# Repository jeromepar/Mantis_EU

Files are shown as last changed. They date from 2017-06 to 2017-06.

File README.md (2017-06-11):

# Mantis_EU

## CNC on a budget **(roughly 220€)**

-------------

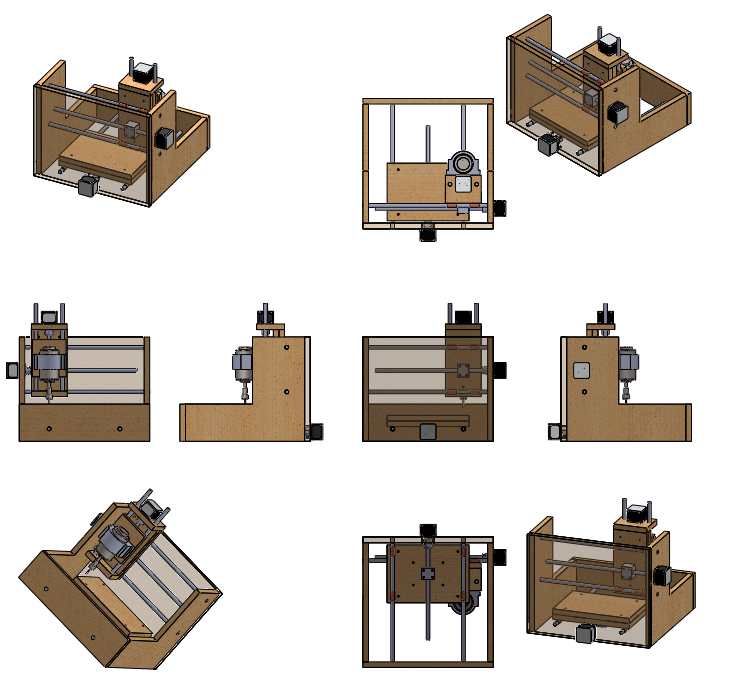
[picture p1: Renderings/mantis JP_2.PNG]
basic rendering


## Adaptation from the Mantis CNC design in order to build it in the EU (dimensions & providers)

### Key information:
- **__Total price around 220€__**
- 350*350mm frame
- *Work area of 100*220mm* (roughly an A5 sheet)
- Frame in 15mm plywood
- Using 3 Nema17 stepper motors
- Controled by an Arduino UNO hosting GRBL
- CNC shield by Protoneer [http://blog.protoneer.co.nz/arduino-cnc-shield/]

### This repository contains:
- CAD parts
- Some rendered pictures
- Some actual pictures
- the B.O.M.

### Basic required hardware:
- Drill press
- **a way to cut wood straight** (circular saw with guide, table circular saw, or jigsaw with skill)

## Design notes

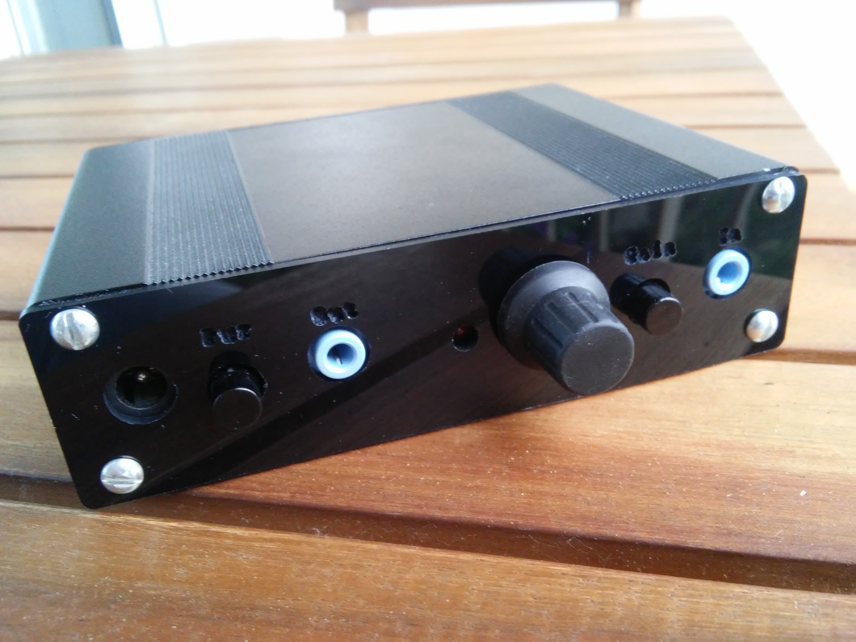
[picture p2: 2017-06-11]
Pictures/20170611_Project1_front_plate.jpg

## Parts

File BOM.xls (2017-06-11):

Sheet: BOM
Nbr | Item | Unit price | Delivery | Total | Comment | Provider | Seller | Article name
1 | Nema17 high torque Z axis | 11 | 0 | 11.00 € |  | ebay | fashionhere (http://www.ebay.fr/usr/fashionhere?_trksid=p2057872.m2749.l2754) | 17HS8401 Nema17 stepper motor 42mm High Torque Hybrid For RepRap CNC 3Dprinter
1 | 5*8 shaft coupling | 3.82 | 0 | 3.82 € |  | aliexpress | CYS bearing | Rigid shaft coupler clamp 5mm to 8mm stepper servo motor coupling D20 l25 5x8mm CNC mill
1 | Stepper motor Nema 17 | 8.38 | 0 | 8.38 € |  | www.ebay.com | mallcolour | Nema 17 1.8° 2 Phase 4-wire 1m Pas A Pas Moteur 1.8Deg CNC 4-wire 1m Cable DIY
1 | end axis switches | 1.26 | 0 | 1.26 € |  | aliexpress | Ali_CanHui | 10 pcs/Lot Poulie commutateur 3 Pied Micro-interrupteur KW11-N Voyage switch KW12 Contacter commutateur KW12-11-N
10 | electric dual wire cable | 0.46 | 0 | 4.60 € |  | aliexpress | Shenzhen Tantan Technologies Co., Ltd | 1m 2m 3m 4m 5m 10m 20m/pcs 22AWG, 2 pin Red Black cable, PVC insulated wire, 22 awg wire Electric cable, LED cable, DIY Connect
2 | A4988 drivers | 0.7 | 0 | 1.40 € |  | aliexpress | BIG TREE TECH Store | 3D printer Bigtree4988 stepper motor drive Stepstick MAX2A with heat sink compatible with A4988 support MAX 128 micro step
1 | M4*30mm screw | 4.56 | 0 | 4.56 € |  | aliexpress | FastKing Store | (50 pc/lot) M2,M2.5,M3,M4 *L =4~50mm grade 10.9 class ISO7380 alloy steel Hex socket button head cap screw
1 | spindle motor | 42.74 | 0 | 42.74 € |  | aliexpress | TwoWin 's Tool Store | Shop Promotions FREE 1pcs ER11 chuck 0.3kw spindle DC 12-48 CNC 300W Spindle Motor Mount Bracket 24V 36V for PCB Engraving
1 | M3*20mm screw | 1.91 | 0 | 1.91 € |  | aliexpress | CuteDigital | 50Pcs M3 Stainless Steel Phillips Screws Cross Round Head M3 Screw Bolts Nuts Fasteners Hardware Tools M3 x6/8/12/14/16/18/20mm
1 | M4*25mm | 5.48 | 0 | 5.48 € |  | aliexpress | FastKing Store | (50 pc/lot) M2,M2.5,M3,M4 *L =4~50mm grade 10.9 class ISO7380 alloy steel Hex socket button head cap screw
1 | M4 washer | 3.39 | 0 | 3.39 € |  | aliexpress | Metal Market | Free shipping 100pcs M4 304 Stainless Steel Flat Washer Plain Washer Flat
1 | M4 Tnuts | 5.02 | 0 | 5.02 € |  | aliexpress | Passion Vienna | 100PCS M4 Metric T Nuts Zinc Plated TEE Nuts 4 Prongs
1 | Arduino Uno board | 2.72 | 0 | 2.72 € |  | aliexpress | WAVGAT Store | Livraison gratuite de haute qualité UNO R3 MEGA328P CH340G pour Arduino Compatible PAS USB CÂBLE MEGA 2560
2 | T8 nut housing | 1.24 | 2.32 | 4.80 € |  | aliexpress | link cnc china Store | T8 trapezoidal screw nut housing white or black mounting bracket aluminum for T8 screw brass nut engraving machine T8 nut 1pcs
1 | 3x8mm Leadscrew + nuts | 11.36 | 0 | 11.36 € |  | aliexpress | BIG TREE TECH Store | RepRap 3D Printer 3pcs THSL-300-8D Lead Screw Dia 8MM Thread 8mm Length 300mm trapezoidal spindle screw with 3PCS copper nut
1 | T8 nut for Z axis | 5.41 | 0 | 5.41 € |  | aliexpress | BIG TREE TECH Store | CNC 3D Printer Parts T8 Anti-Backlash Nut Block+M4 Set Screw For Openbuilds T8 8mm Lead Screw 3D0273+LS030
3 | 8mm*5mm coupler | 0.91 | 1.58 | 4.31 € |  | aliexpress | link cnc china Store | D20 L20 hole minimum 2mm maximum 10mm rigid coupling shaft rod coupler section cnc stepper motor carving machine screw 1pcs
1 | 50 bushings | 6.69 | 0 | 6.69 € |  | aliexpress | IMI Industry | 42L-52 Free shipping SF1 10*12*25 mm SF1-1025 composite oil bushing copper sleeve self-lubricating bearing
3 | 10 M3 Tnuts | 0.58 | 0 | 1.74 € |  | aliexpress | Top Guardian | M3x6mm 10pcs/Set Four Prong Furniture T Nut Inserts For Wood Zinc Plated Prevent Rust
1 | 5x Polulu a4988 drivers | 10.99 | 0 | 10.99 € | the previous ones died … | amazon | Elegoo | Elegoo POLOLU Module A4988 Stepstick Pilote de Moteur Pas à Pas + Radiateur. Pour Imprimantes 3D REPRAP, Machines CNC ( Commande Numériques ), Robots ou Arduino( Pack de 5 ) Stepper Motor Driver Module + Heat Sink for 3D Printer
1 | 5*8mm flexible coupler | 2.48 | 0 | 2.48 € |  | elecrow |  | Stepper Motor Flexible Coupling Coupler 5*8MM
1 | Grbl shield for arduino Uno | 20 | 0 | 20.00 € |  | elecrow | protoneer | protoneer Arduino CNC Shield V3.51 - GRBL v0.9 compatible
1 | 15mm plywood | 40 | 0 | 40.00 € | 160x80cm | Leroy Merlin
1 | M6 Tnuts | 3 | 0 | 3.00 € |  | Leroy Merlin
6 | round rail for axis 35mm | 0 | 0 | 0.00 € | Already in stock
1 | Epoxy glue | 10 |  | 10.00 € |  | Leroy Merlin
 |  |  | = | 217.06 €
 | Unused
Nbr | Item | Unit price | Delivery | Total | Comment | Provider | Seller | Article name
2 | Stepper motor Nema 17 | 8.38 | 0 | 16.76 € | 1 with uncentered axis, the other didn't had enough torque for Z axis | www.ebay.com | mallcolour | Nema 17 1.8° 2 Phase 4-wire 1m Pas A Pas Moteur 1.8Deg CNC 4-wire 1m Cable DIY
1 | Arduino Mega board | 7.04 | 0 | 7.04 € |  | www.ebay.com | tim-hpx (http://www.ebay.fr/usr/tim-hpx?_trksid=p2047675.l2559) | ATmega2560-16AU Improved version CH340G MEGA2560 R3 Board For Arduino UNO TMPG
1 | Nema17 mounting bracket | 2.7 | 0 | 2.70 € |  | aliexpress | Men's Wardrobes | 1PC 42mm L Shape Alloy Steel Mounting Bracket For NEMA17 Stepper Motor 5X5X5cm(L*W*H)
 |  |  | = | 26.50 €

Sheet: ref Parts (from another build)
Qty | P/N | Description | Supplier | Price | Ext | Note
Spindle
1 | 5234K72 | Nylon/silicone tubing coupler | McMaster | $0.25 | $0.25 | per foot - 1 foot
2 | R4ZZ-ABEC3 | .25" ID .625" OD bearing | Ebay | $4.44 | $8.88 | R4-ZZ Premium Bearing 1/4 x 5/8 R4 ZZ, ABEC 3 |  | Buyer: jjdini3
1 | AAS-A4-17 | .25x3.00" shaft | ServoCity | $3.25 | $3.25
1 | 2868T17 | .625x.75x1" bronze bushing | McMaster | $0.93 | $0.93
1 | CDS-B1-4 | 1/8" to 1/4" Rigid Coupling | ServoCity | $10.66 | $10.66
1 | 9414T6 | .25" shaft collar | McMaster | $0.58 | $0.58
1 | 94639A189 | .09x.25x.3125" spacer | McMaster | $7.99 | $7.99 | 100 pack
2 |  | 1/64" End Mill Bits | Ebay | $7.40 | $14.80 | 1/64" 2fl SINGLE END CARBIDE END MILL |  | Buyer: roginsf
2 |  | 1/32" End Mill Bits | Ebay | $6.00 | $12.00 | 1/32" 2fl SINGLE END CARBIDE END MILL |  | Buyer: roginsf
1 | 5234K77 | Nylon/silicone tubing coupler 5/16" ID | McMaster | $1.22 | $1.22 | per foot - 1 foot |  | I may use this for a flexible coupling between the steppers and the threaded rod
1 | 98381A478 | Steel Dowel Pin 1/8" Dia. 1.5" Length | McMaster | $5.97 | $5.97 | 50 pack
Linear
4 | 6061K108 | .375x10" precision rod | McMaster | $4.86 | $19.44
2 | 6061K422 | .375x7" precision rod | McMaster | $4.17 | $8.34
12 | 2868T72 | .375x.5x.625" 863 bronze bushings | McMaster | $0.56 | $6.72
1 | 98935A817 | 3/8-12 lead screw 36" 2G | McMaster | $5.00 | $5.00
3 |  | 3/8-12 Acme Flange Nuts | Ebay | $5.00 | $15.00 | 3/8-12 Acme Flange Nut CNC Router Mill Lead Screw |  | Buyer: mjs-enterprises-66
Hardware
1 | 90283A112 | 4-40x.625" flat pan head screws | McMaster | $1.56 | $1.56 | 100 pack
1 | 92949A199 | 8-32x1" screws allen button head | McMaster | $8.05 | $8.05 | 100 pack
1 | 90975A012 | 8-32 tee nuts | McMaster | $6.74 | $6.74 | 100 pack
1 | 90126A512 | 8-32 washer | McMaster | $1.29 | $1.29 | 100 pack
1 | 90252A104 | #6x.75" plywood screw phillips | McMaster | $6.66 | $6.66 | 100 pack
1 |  | Loctite 638 | Ebay | $22.10 | $22.10 | LOCTITE 638 HIGH STRENGH RETAINER 50ML MAY 2012 EXP (http://cgi.ebay.com/ws/eBayISAPI.dll?ViewItem&item=180571335950&ssPageName=STRK:MEWNX:IT) |  | Buyer: stalyvegassam
1 | 92005A076 | M2.5 16mm L, 0.45mm Pitch phillips pan head screws | McMaster | $3.64 | $3.64 | 100 pack
1 |  | Loctite 5 min Epoxy | Lowes | $3.97 | $3.97 | 1 double mix syringe 0.85 fl Oz.
1 |  | Gorilla Glue - Fast Cure - White | Lowes | $4.99 | $4.99 | 2 fl Oz. bottle
1 |  | Loctite 30 min Epoxy | Lowes | $3.97 | $3.97 | 1 double mix syringe 0.85 fl Oz.
Electronics
3 | 28M056 | Nema 17 steppers | Ebay | $7.97 | $23.91 | LIN ENGINEERING 4118 SMALL STEPPING MOTOR NEMA 17 |  | Buyer: supertechshop
1 |  | TB6560 Driver | Ebay | $76.98 | $76.98 | CNC 3 axis Stepper motor Driver TB6560 INCLUDES EXTRAS |  | Buyer: carolbrent
1 |  | 12 VDC Power Supply | Ebay | $44.99 | $44.99 | CNC STEPPER MOTOR POWER SUPPLY 12vdc 8.5amp 100 watts |  | Buyer: carolbrent
1 | MD5-2445 | 12 VDC 2 Amp 19,050 RPM Motor | Ebay | $8.00 | $8.00 | Small DC Electric Motor 12 VDC 19850 RPM 80 G-cm - M41 (http://cgi.ebay.com/ws/eBayISAPI.dll?ViewItem&item=360302316807&ssPageName=STRK:MEWNX:IT) |  | Buyer: joe_wv55
Wood
1 |  | 2' x 4' 1/2" Birch | Home Depot | $13.97 | $13.97 | Quarter Sheet Handy Panel | I purchased this for extra wood to make a small cabinet base
1 |  | 2' x 2' 1/2" Birch | Lowes | $7.97 | $7.97 | Eigth Sheet Handy Panel | This is enough to make entire Mantis machine
 |  |  | TOTAL | $359.82
 |  |  | ServoCity: | http://www.servocity.com/index.html
 |  |  | McMaster-Carr | http://www.mcmaster.com
 |  |  | eBay | http://ebay.com
 |  |  | Lowes | Local pickup - Find a local store at: http://lowes.com
 |  |  | Home Depot | Local pickup - find a local store at: http://homedepot.com

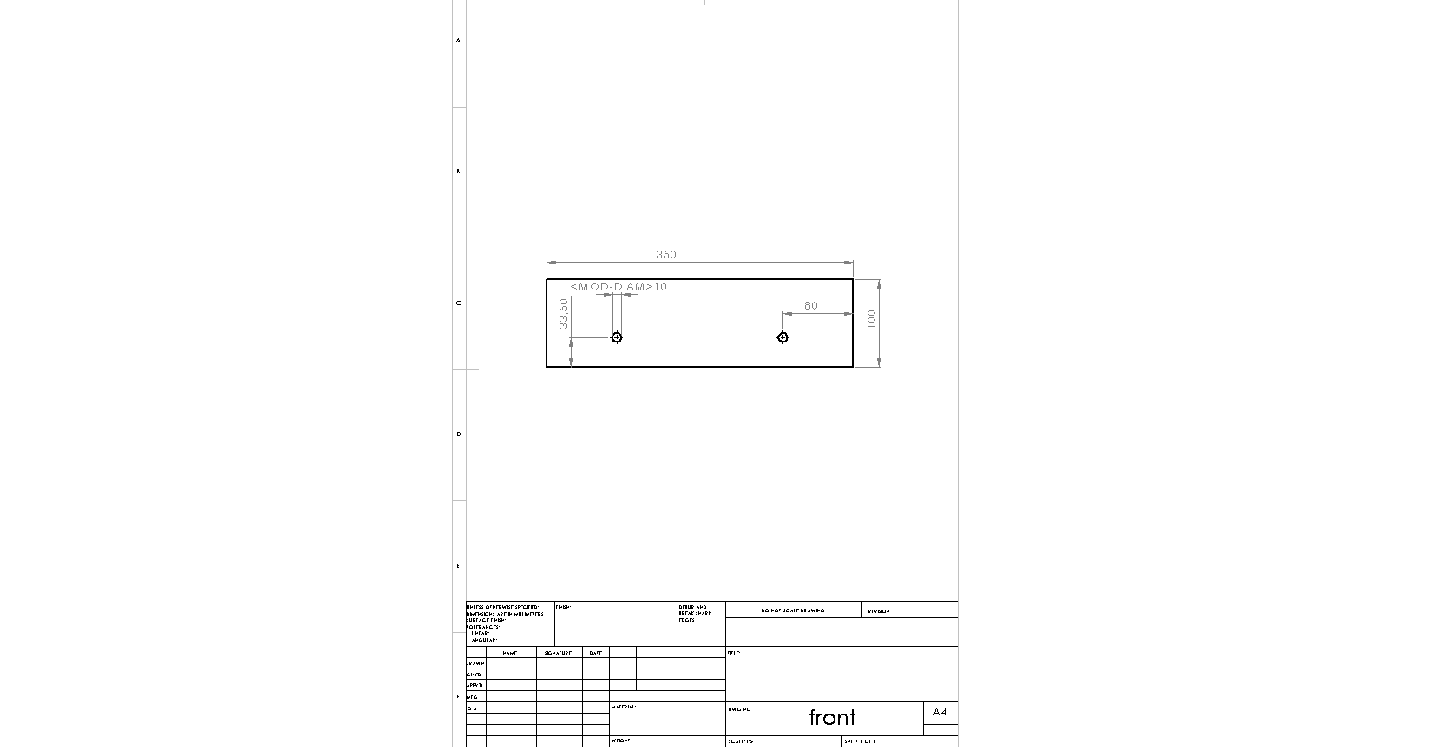
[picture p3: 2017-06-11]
CAD/solidworks/parts/front.PNG

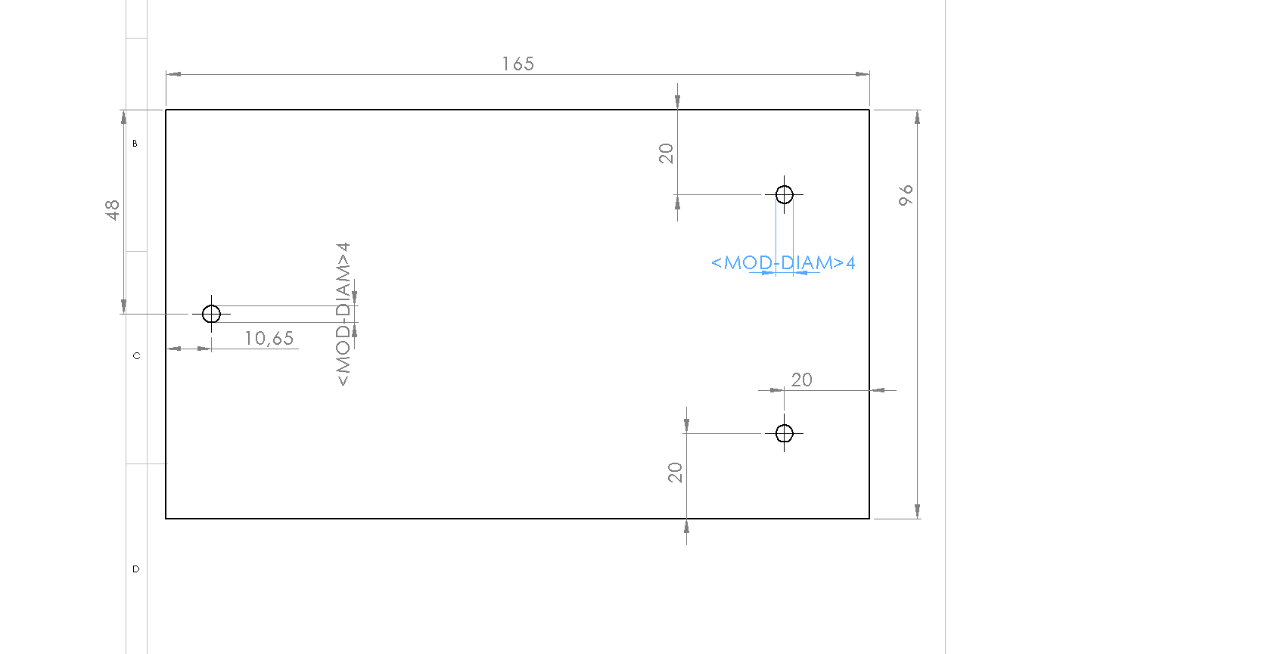
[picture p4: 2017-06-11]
CAD/solidworks/parts/ZBackbis.PNG

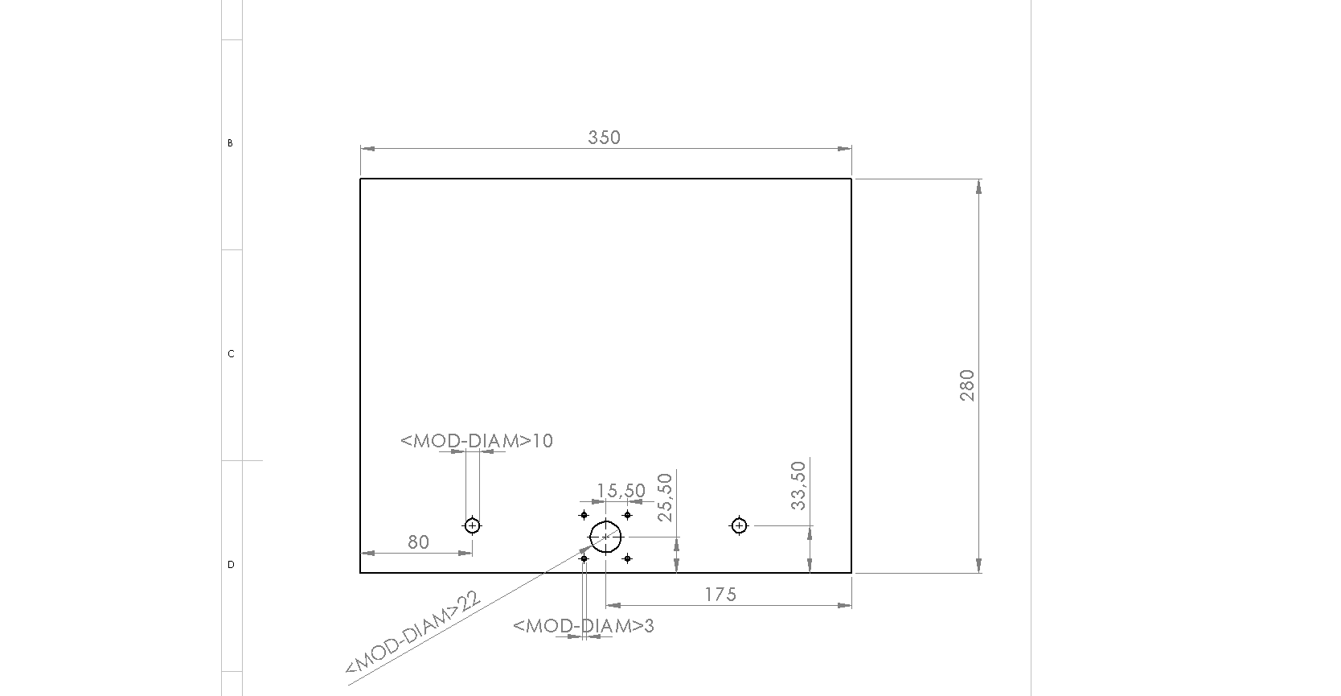
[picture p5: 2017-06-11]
CAD/solidworks/parts/back.PNG

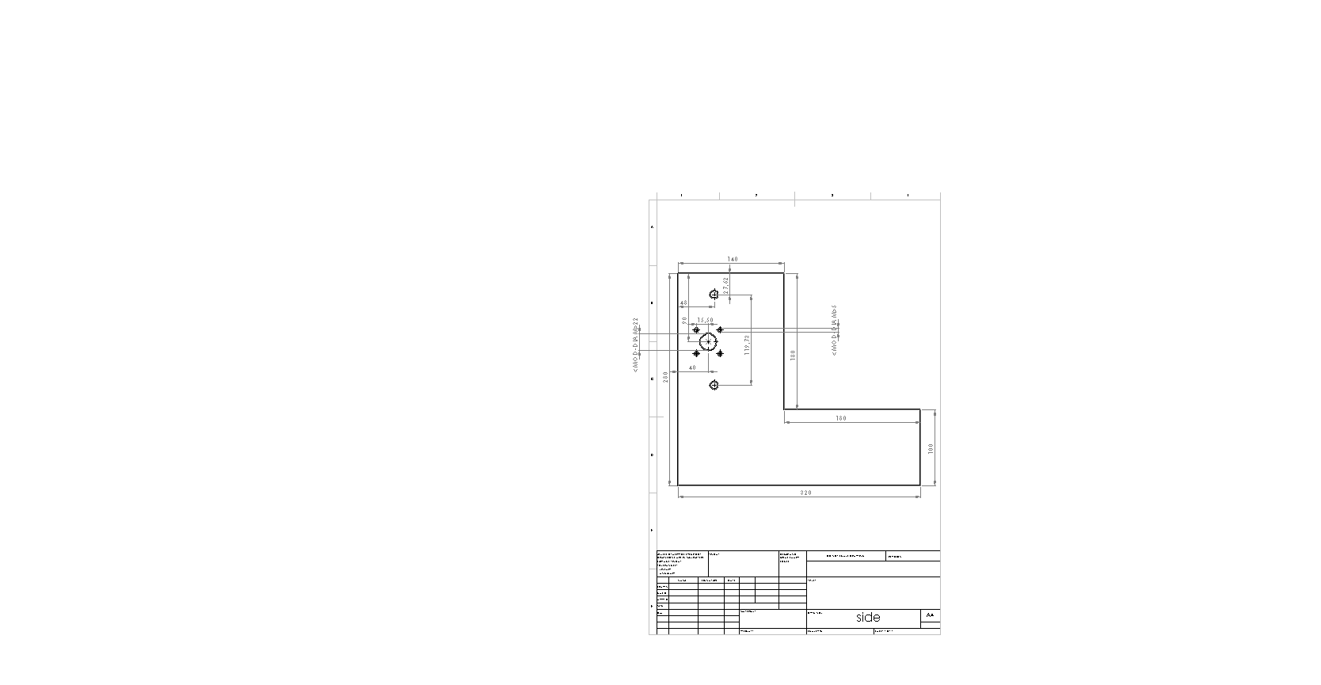
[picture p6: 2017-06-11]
CAD/solidworks/parts/side.PNG

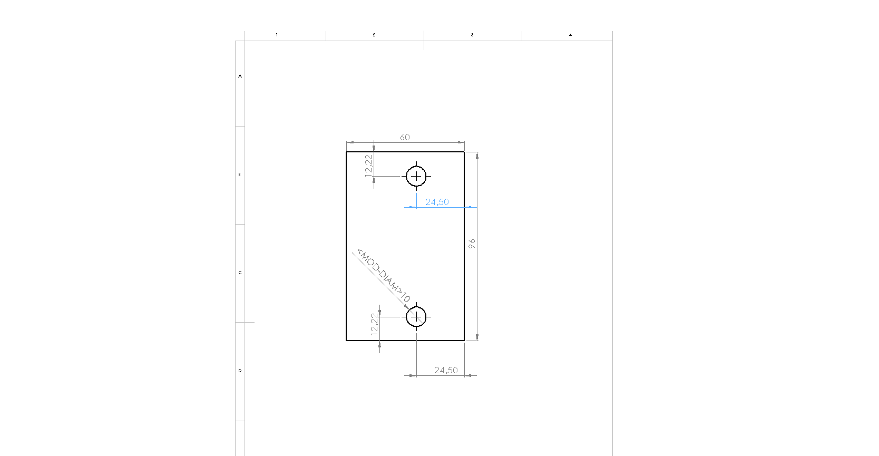
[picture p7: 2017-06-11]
CAD/solidworks/parts/Zbottom.PNG

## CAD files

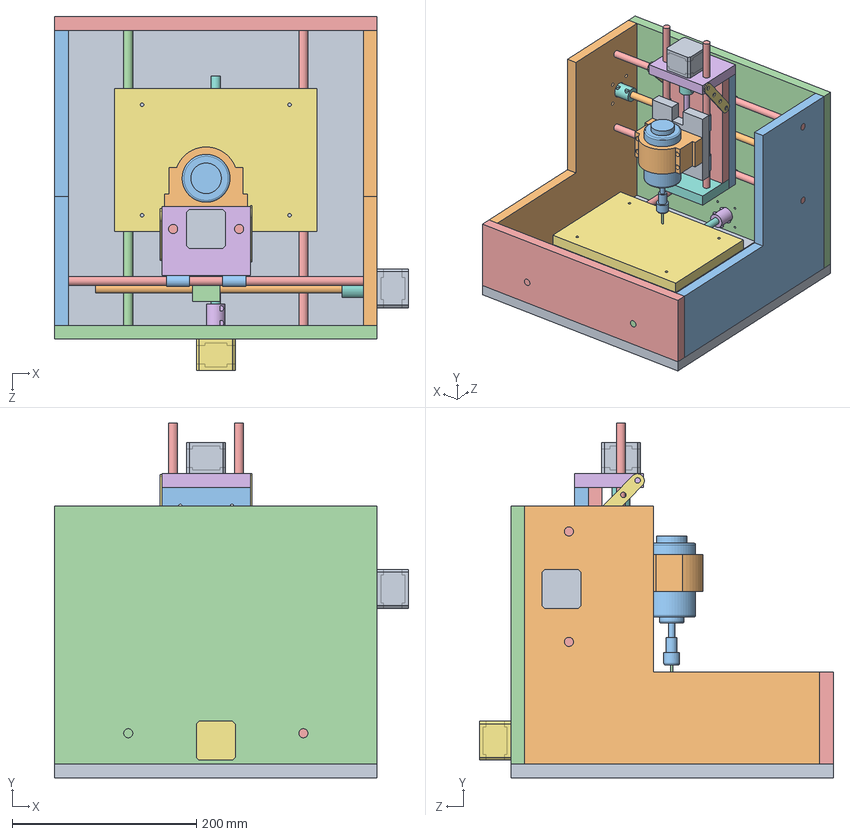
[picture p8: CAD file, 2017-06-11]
CAD/solidworks/mantis JP_2.SLDASM
384.0 x 385.0 x 384.0 mm
bottom
side
Copy (2) of side^mantis JP_2
back
front
Copy of stepper coupler^mantis JP_2
NEMA 17 Stepper Motor2
Copy of screw Y1^mantis JP_2
permanent_plate
Copy of bushing^mantis JP_2
bushing^mantis JP_2 x 11
Copy of lin_axe^mantis JP_2
lin_axe^mantis JP_2 x 3
Copy of block mount^mantis JP_2
sacrificial bed^mantis JP_2
stepper coupler^mantis JP_2 x 2
NEMA 17 Stepper Motor x 2
screw Y1^mantis JP_2
Zback
ZBackbis
Ztop
Copy of Part4^mantis JP_2
Zbottom
ZbackFinal
100mm spindle clamp 3kw
motor^mantis JP_2
spindle^mantis JP_2
Zslider^mantis JP_2 x 2
Zscrew^mantis JP_2
barre^mantis JP_2 x 2

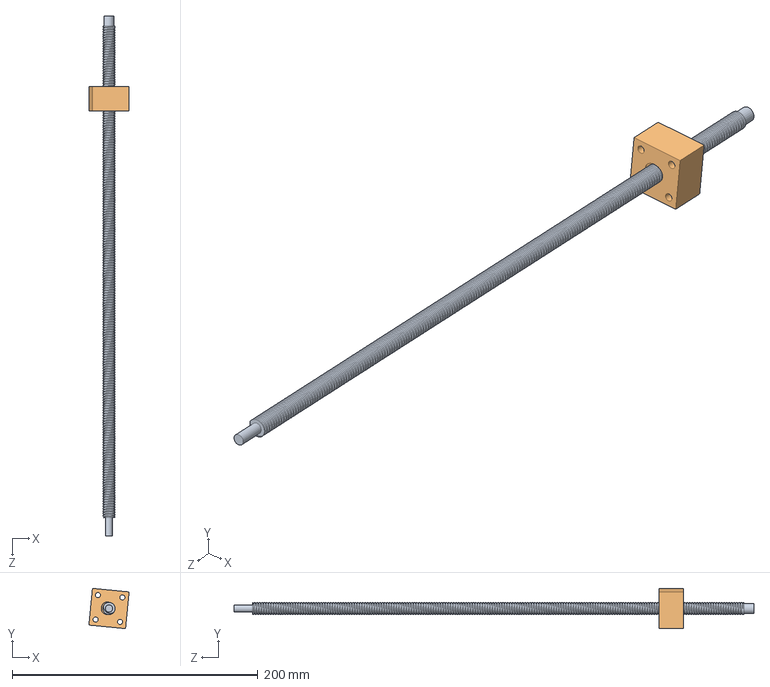
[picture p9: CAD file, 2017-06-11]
CAD/solidworks/model imported/TrapezoidalAssembly.SLDASM
32.7 x 32.7 x 423.0 mm
Trapezoidal thread423mm
Trapezoidal Nut

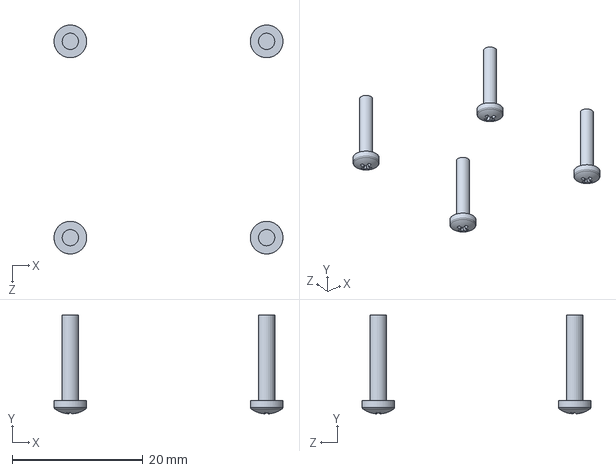
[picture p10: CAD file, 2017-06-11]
CAD/solidworks/model imported/NEMA 17 Stepper Motor Assembly.SLDASM
35.0 x 15.1 x 35.0 mm
pan cross head_am x 4

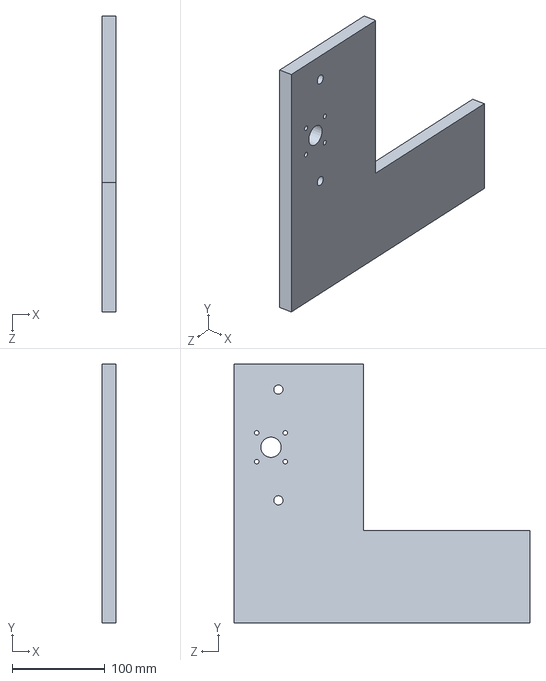
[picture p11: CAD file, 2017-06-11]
CAD/solidworks/parts/side.SLDPRT
15.0 x 280.0 x 320.0 mm

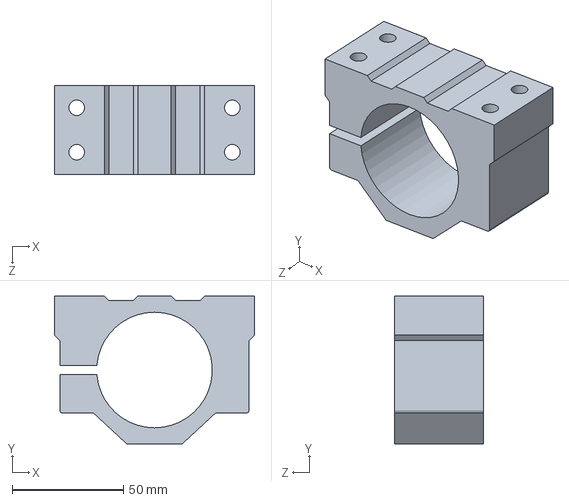
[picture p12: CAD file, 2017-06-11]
CAD/solidworks/model imported/SPH52mm.SLDPRT
90.0 x 66.5 x 40.0 mm

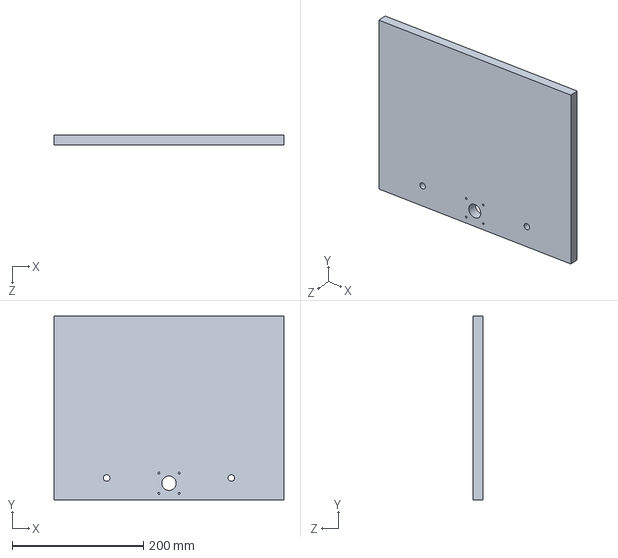
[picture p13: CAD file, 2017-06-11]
CAD/solidworks/parts/back.SLDPRT
350.0 x 280.0 x 15.0 mm

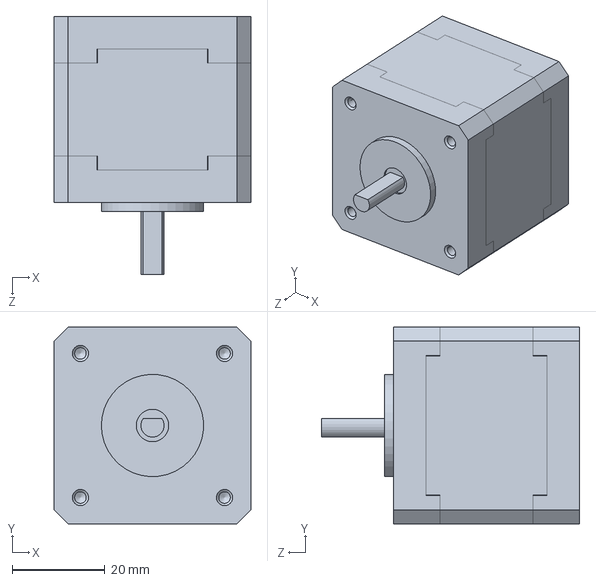
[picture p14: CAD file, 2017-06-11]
CAD/solidworks/model imported/NEMA 17 Stepper Motor2.SLDPRT
42.3 x 42.3 x 55.5 mm

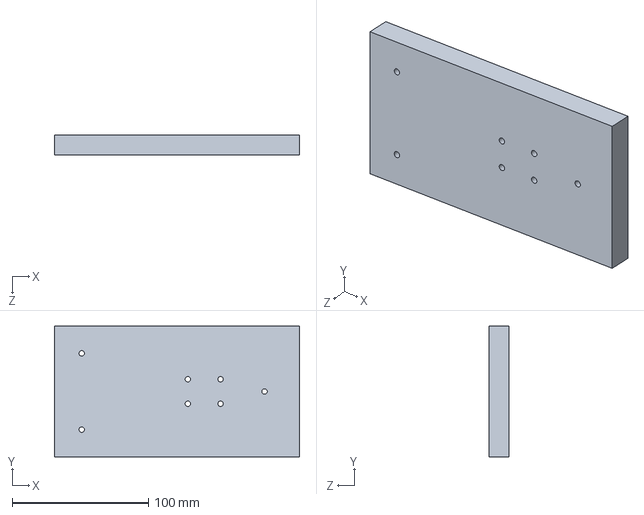
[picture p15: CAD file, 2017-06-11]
CAD/solidworks/parts/Zback.SLDPRT
180.0 x 96.0 x 15.0 mm

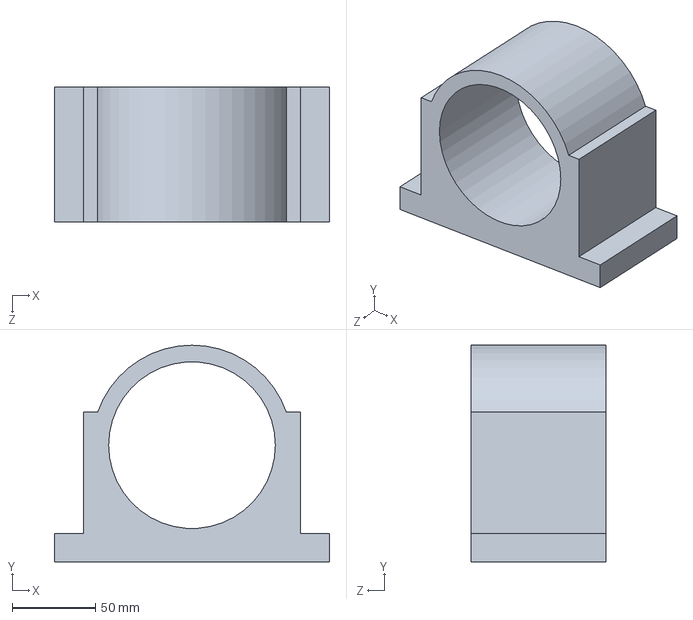
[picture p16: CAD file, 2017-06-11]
CAD/solidworks/model imported/100mm spindle clamp 3kw.SLDPRT
165.0 x 130.0 x 81.0 mm

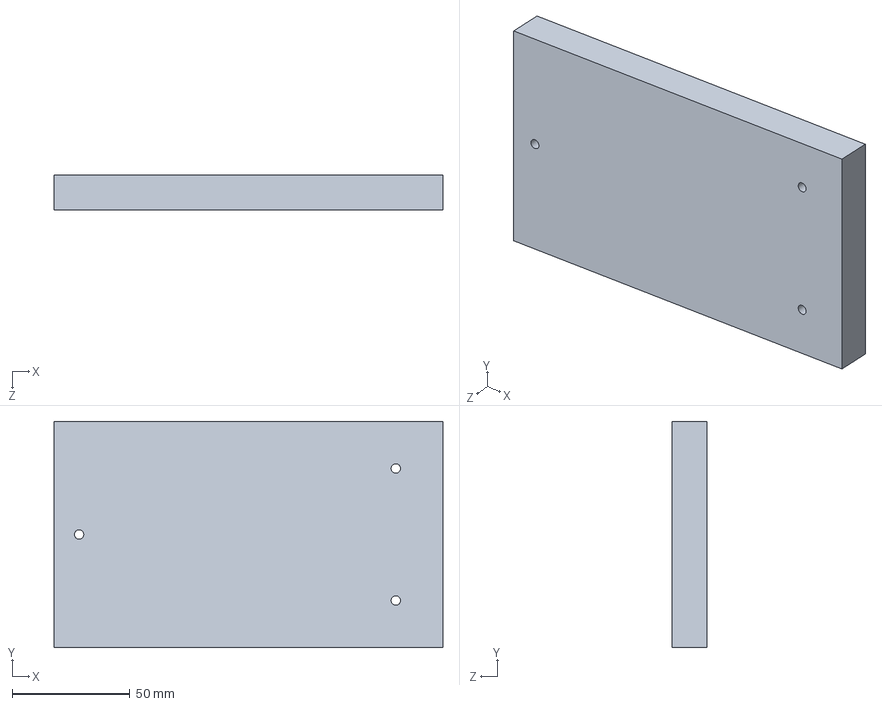
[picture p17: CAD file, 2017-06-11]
CAD/solidworks/parts/ZBackbis.SLDPRT
165.0 x 96.0 x 15.0 mm

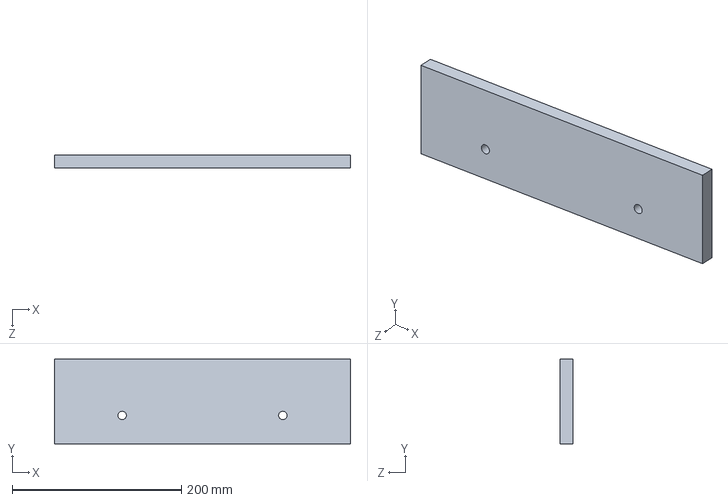
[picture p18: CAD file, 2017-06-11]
CAD/solidworks/parts/front.SLDPRT
350.0 x 100.0 x 15.0 mm

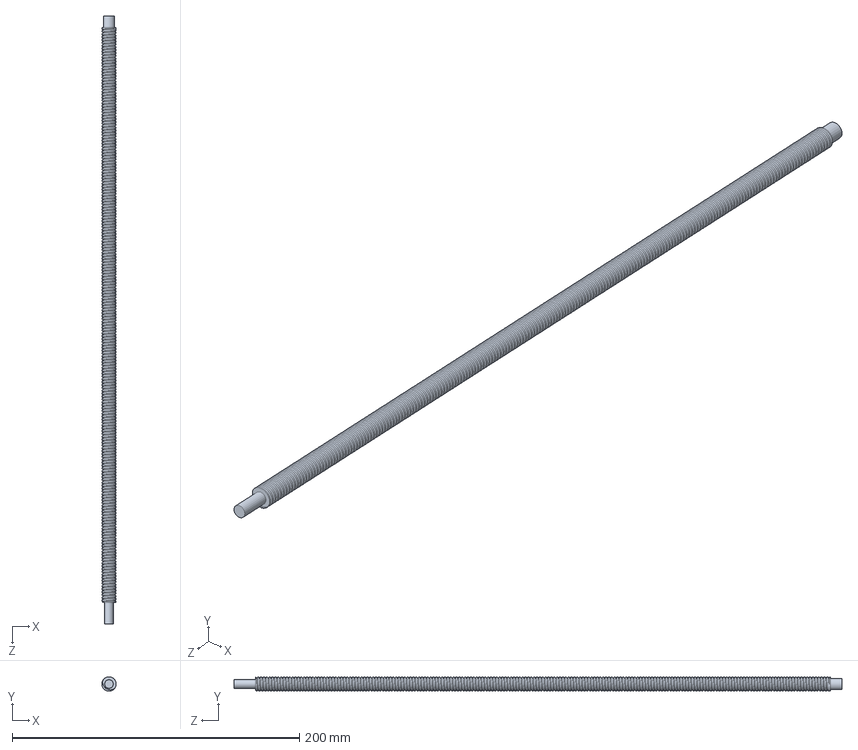
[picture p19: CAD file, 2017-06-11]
CAD/solidworks/model imported/Trapezoidal thread423mm.SLDPRT
10.0 x 10.0 x 423.0 mm

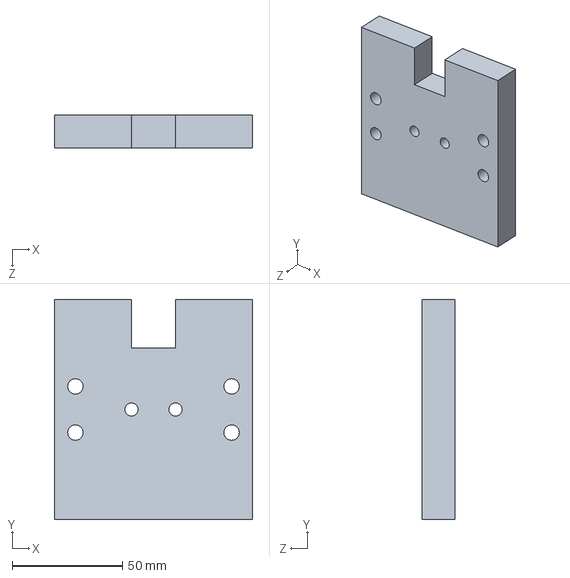
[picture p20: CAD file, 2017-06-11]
CAD/solidworks/parts/ZbackFinal.SLDPRT
90.0 x 100.0 x 15.0 mm

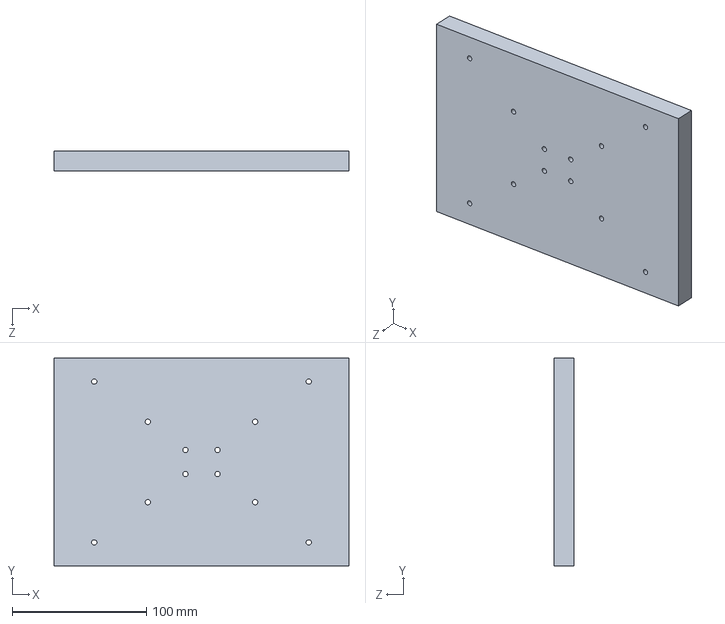
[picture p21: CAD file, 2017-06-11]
CAD/solidworks/parts/permanent_plate.SLDPRT
220.0 x 155.0 x 15.0 mm

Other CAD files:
CAD/solidworks/model imported/NEMA 17 Stepper Motor.SLDPRT
CAD/solidworks/parts/Ztop.SLDPRT
CAD/solidworks/parts/Zbottom.SLDPRT
CAD/solidworks/parts/bottom.SLDPRT
CAD/solidworks/mantis JP_2.SLDDRW
CAD/solidworks/model imported/SMK52.ipt
CAD/solidworks/model imported/Trapezoidal Nut.SLDPRT
CAD/solidworks/parts/ZBackbis.SLDDRW
CAD/solidworks/parts/Zback.SLDDRW
CAD/solidworks/parts/ZbackFinal.SLDDRW
CAD/solidworks/parts/Zbottom.SLDDRW
CAD/solidworks/parts/Ztop.SLDDRW
CAD/solidworks/parts/back.SLDDRW
CAD/solidworks/parts/bottom.SLDDRW
CAD/solidworks/parts/front.SLDDRW
CAD/solidworks/parts/permanent_plate.SLDDRW
CAD/solidworks/parts/side.SLDDRW

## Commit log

2017-06-10 Importation
    BOM not updated
    [100mm spindle clamp 3kw.SLDPRT, BOM.xls, NEMA 17 Stepper Motor Assembly.SLDASM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]
2017-06-11 BOM updated & Pictures added
    [BOM.xls]
2017-06-11 Updated for delivery
    [BOM.xls]
